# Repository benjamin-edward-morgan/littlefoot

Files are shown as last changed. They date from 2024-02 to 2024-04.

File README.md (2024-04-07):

# littlefoot
This is a repo documenting the modification of an old remote controlled car to include a Raspberry pi, a camera and some sensors that allow it to be teleoperated over a wifi connection. It serves as a testbed for [IOC](https://github.com/benjamin-edward-morgan/ioc), which I am developing as a more general purpose teleoperation software package. 

So they wouldn't go to waste, this project uses some discontinued parts that I just happened to have lying around. The 3d printed parts also are specific to this particular model of RC car and my modifications to it. As such, this should serve as more of an example to inform future designs, rather than something intended to be reproduced identically.

### Overview 
- **[IOC](https://github.com/benjamin-edward-morgan/ioc)**
The core application is implemented in Rust. It serves the mjpeg stream, the websocket, and communicates with the i2c devices.
- **[config](config/README.md)**
Contains the config files for IOC. The config file specifies what hardware is attached and how it is controlled. 
- **[littlefoot-ui](littlefoot-ui/README.md)**
A UI implemented in React and TSX. It connects to the websocket and displays the mjpeg stream, sensor outputs and allows driving and looking. Includes a touch UI for touch capable devices, and a keyboard-based interface for desktop.
- **[parts](parts/README.md)**
Openscad design and `.stl` renders for 3d printed parts used in this build.

| Fully Assembled | Interface |
| --- | --- |
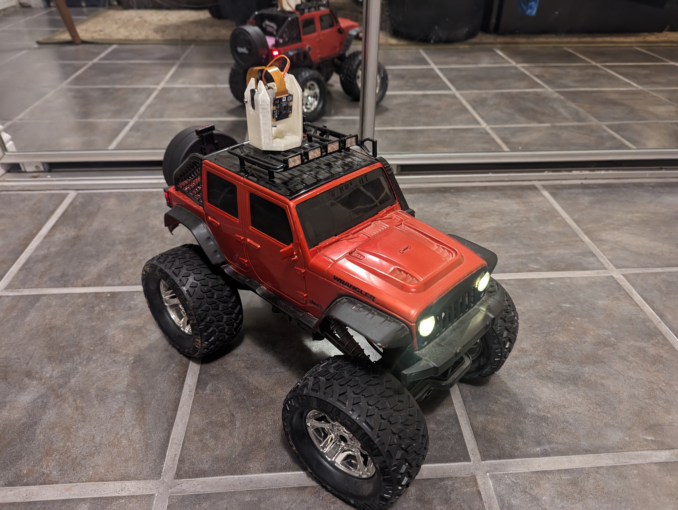
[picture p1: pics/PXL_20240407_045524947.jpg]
littlefoot assembled and running
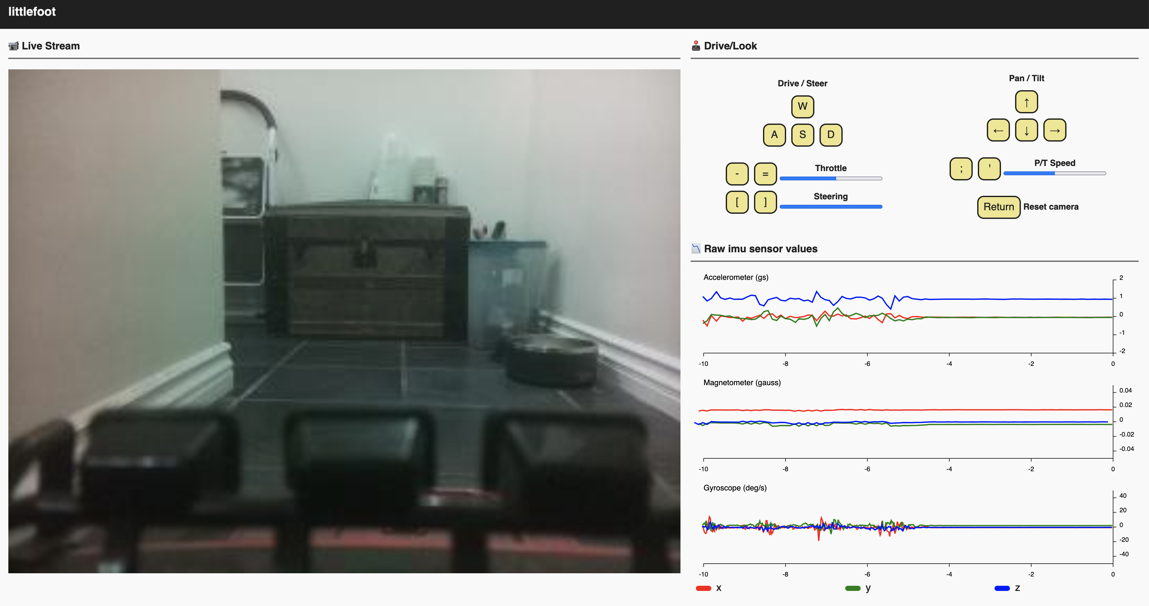
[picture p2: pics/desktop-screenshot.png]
littlefoot-ui interface
|  |  |

### Features 
- Connection over local wifi connection to a web interface
- Live video feed from the camera, in the form of an mjpeg stream
- Camera can be panned and tilted about 180 degrees
- Camera settings can be adjusted in real time
- Accelerometer, Gyroscope and Magenetometer are charted in real time
- Barometric pressure and temperature are displayed in real time (just threw that in there for fun since it was already included on the 10 DOF board)
- Headlights and taillights are independently controllable and dimmable

### Parts list
- 1x old ["New Bright" RC Jeep](https://www.newbright.com/products/rc-heavy-metal-jeep-wrangler/), with exising circuit board removed.
- 1x [Raspberry PI Zero W](https://www.raspberrypi.com/products/raspberry-pi-zero-w/), whith headers soldered on.
- 1x [Raspberry PI Camera V2.1](https://www.raspberrypi.com/products/camera-module-v2/) NoIR and [30cm ribbon rable](https://www.amazon.com/gp/product/B07H3L3LM2/ref=ppx_yo_dt_b_asin_title_o01_s00?ie=UTF8&th=1) for Pi Zero.
- 1x microSD card (overkill at 64gb)
- 3x [18650 batteries](https://www.18650batterystore.com/products/samsung-30q), and [holders](https://www.amazon.com/HiLetgo-10pcs-Battery-Holder-Storage/dp/B00LSG5BKO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)
- 1x [battery protection board](https://www.amazon.com/Battery-Protection-Lithium-Charger-Charging/dp/B09B335Q4P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)
- 1x [DC/DC voltage converter](https://www.sparkfun.com/products/9370) and trim resistor(s) to get 5v
- 1x [PCA9685 breakout](https://www.adafruit.com/product/815) (pwm output)
- 1x discontinued [10 DOF board](https://www.adafruit.com/product/1604) with L3GD20H, LSM303, and BMP180
- 1x [L298N dual h-bridge](https://www.sparkfun.com/products/9479)
- 4x LEDs (2 red and 2 white)
- 3S [battery level indicator](https://www.amazon.com/gp/product/B07T5RBF5V/ref=ppx_yo_dt_b_asin_title_o02_s00?ie=UTF8&th=1) 
- DC Barrel jack and [3S Li-Ion charger](https://www.amazon.com/gp/product/B086ZFHVX9/ref=ppx_yo_dt_b_asin_title_o01_s00?ie=UTF8&psc=1)
- Diodes, resistors and a couple capacitors. 
- Perf board, wire, connectors, crimp connectors, hot glue, 3mm nuts and bolts.
- 3d printed brackets for perf boards, pan/tilt mechanism.

### Learnings (so far...)
- The RC car does not have great meanuverability. It has two discrete steering radii, rathern than a continuous range. The smallest turning radius is still on the order of 1 meter. This is entirely due to New Bright's design of the steering linkage which limits the steering range.
- The capacitor in parallel with the power supply to the L298N is necessary to protect the chip. Once, it ran into a wall at full speed without the capacitor and half of the chip was fried. It was a real pain to replace.
- The old Raspberry Pi V2 camera has a decent field of view, but the new wide angle v3 camera should be better.
- You should take care to not push a servo beyond its limit. On another occasion the pan servo (which should only have a 180 degree range) was pushed too far in one direction. The servo unexpectely performed a full rotation, wrapping the ribbon cable around the camera and tilt mechanism until the servo and camera were unplugged. This unfortunately damaged the ribbon cable and connector on the Raspberry Pi.  
- Would be nice to sense the battery voltage. The only way to get a battery reading is to view the indicator on the physical car. 
- The DC motors for drive and steer do create noticible noise in the magnetometer readings.
- Internal temperature sensor rises about 10 degrees C above ambient when the car is running, due to the heat generated by the Raspberry Pi.

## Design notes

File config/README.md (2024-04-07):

## Config 
- `littlefoot.yml` 
This is the file used on the actual robot with live hardware
- `littlefoot-dev.yml`
This is used for local development. It is compatible with a build of IOC that does not include the hardware drivers.

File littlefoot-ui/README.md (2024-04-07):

### littlefoot-ui 
This is web UI using React that acts as the remote control and shows the camera live feet, telemetry data etc. See [README_VITE.md](README_VITE.md) for more information about vite + react. 

This expects:
- /ws to be an ioc websocket url
- /stream to be an mjpeg stream

It should be packaged with `npm run build` and placed in the `assets` directoy on the raspberry pi, alongside littlefoot.yml and the ioc binary. 

You can also use `npm run dev` and run the IOC sever locally. By default npm will proxy to `localhost:8080` but that can be configured in `vite.config.ts`

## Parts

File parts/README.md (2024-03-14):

### parts 

These are some 3d printed parts I whipped up:
- pan/tilt mechanism based on 1 regular and one micro servo 
- adapter to perf boards to rc jeep body, spacers between perf boards 
- protective plastic parts to enclose another perf board for battery protection board

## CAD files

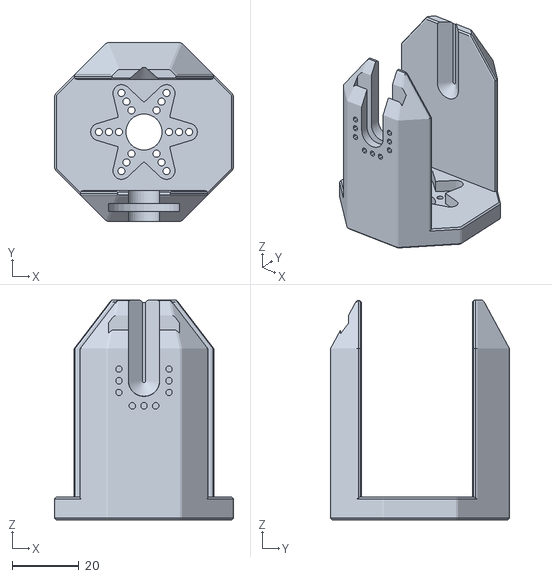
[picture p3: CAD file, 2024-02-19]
parts/stl/pantilt-bracket.stl
53.6 x 53.6 x 65.8

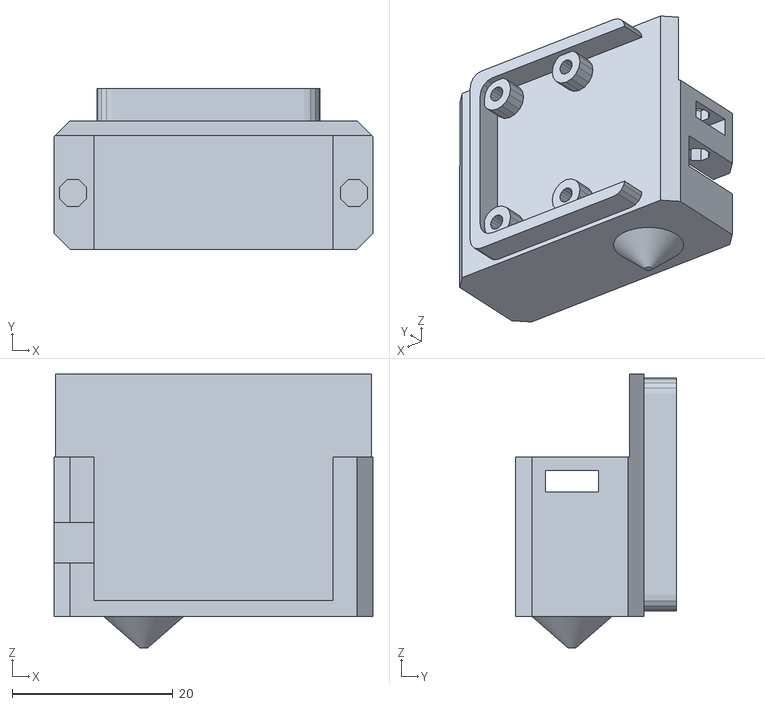
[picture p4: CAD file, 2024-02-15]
parts/stl/cam-bracket.stl
39.8 x 20.0 x 34.1

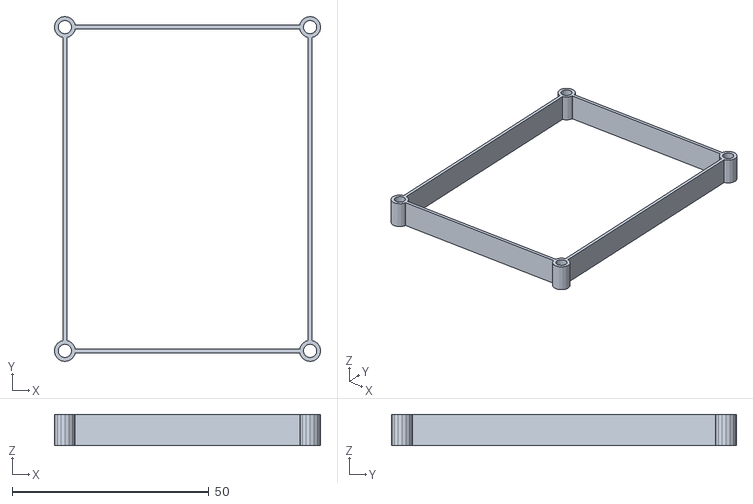
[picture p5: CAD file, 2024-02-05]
parts/stl/spacer1.stl
67.8 x 87.8 x 8.00

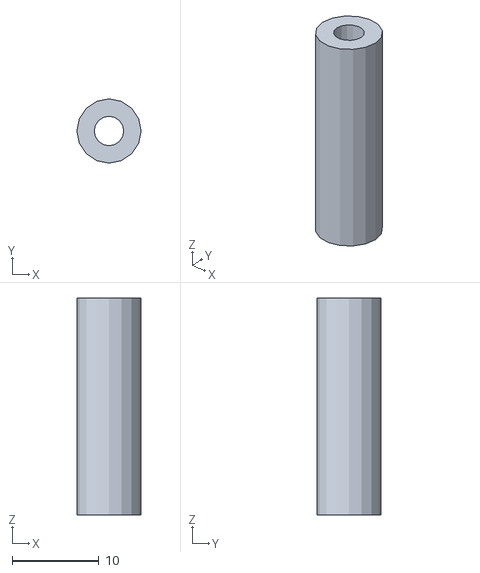
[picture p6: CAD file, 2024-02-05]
parts/stl/spacer.stl
7.40 x 7.40 x 25.0

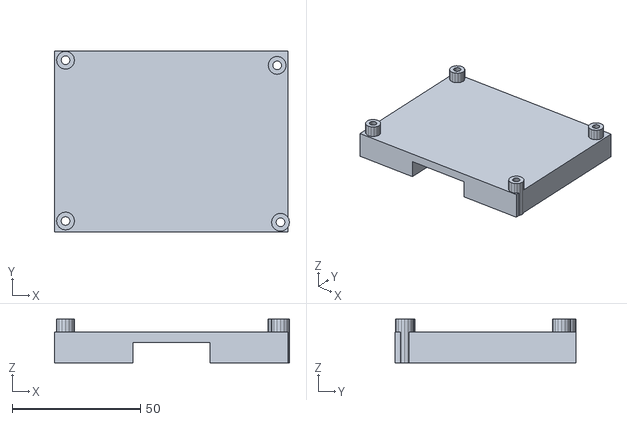
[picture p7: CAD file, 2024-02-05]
parts/stl/power_board_bottom.stl
91.5 x 70.5 x 17.0

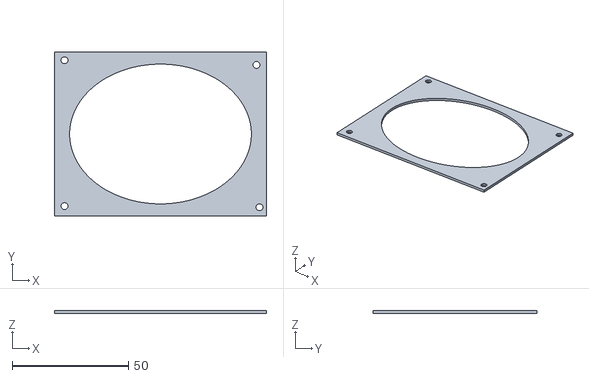
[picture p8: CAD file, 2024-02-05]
parts/stl/board-test.stl
91.0 x 70.5 x 1.20

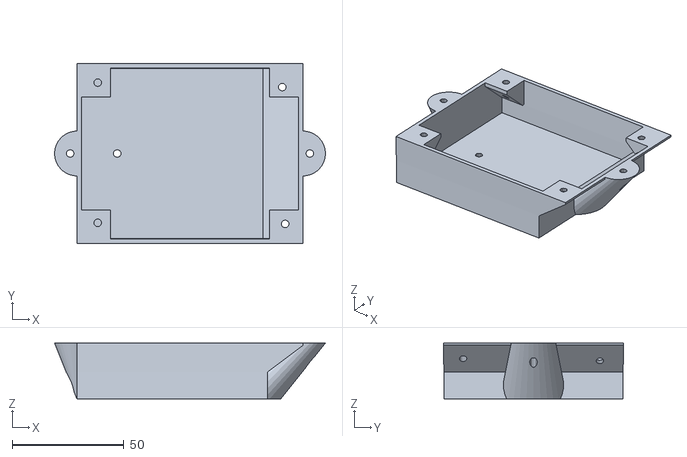
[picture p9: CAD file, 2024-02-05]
parts/stl/electronics-base.stl
121.0 x 80.5 x 25.0

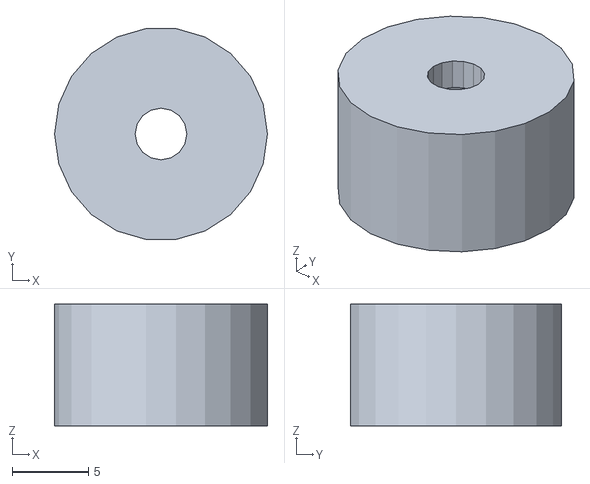
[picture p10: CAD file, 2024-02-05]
parts/stl/captured-nut-test.stl
14.0 x 13.9 x 8.00

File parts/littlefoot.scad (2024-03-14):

//apologies for this sloppy scad code. ~b


//electronics enclosure 
base_w = 80;
base_l = 85;
base_screw_y_offs = 18;
base_screw_d = 3;
base_t = 4;
wall_t = 2;
xy_clearence = 3;
xy_tol = 0.2;

//body (jeep)
body_rear_mount_w = 91;
body_rear_mount_z = 12;
body_rear_mount_x = -80; 
body_front_mount_w = 67;
body_front_mount_z = 32;
body_front_mount_x = 140;
interior_clearence = 52;

//electronics 
perf_board_w = 70.5;
perf_board_l = 91;
perf_board_t = 1.2; 
perf_board_hole_d = 3;
perf_board_holes = [
    [-perf_board_l/2+4.3, -perf_board_w/2+4.3],
    [-perf_board_l/2+4.3, perf_board_w/2-3.6],
    [perf_board_l/2-4.3, perf_board_w/2-5.6],
    [perf_board_l/2-3, -perf_board_w/2+3.8],
];



enclosure_w = perf_board_w + 2*(xy_clearence + wall_t);
enclosure_l = perf_board_l + 2*(xy_clearence + wall_t);
enclosure_x_offs = 8;
enclosure_z_offs = 12;
enclosure_h = 50;

//hardware
bolt_d = 3;
nut_w = 5.4;
nut_r = nut_w/(2*cos(30));
nut_h = 2.27;
nut_tol = nut_h + xy_tol + wall_t;



std_srvo_body_w = 20.33;
std_srvo_body_l = 40.78;
std_srvo_body_h = 38.04;
std_srvo_bracket_l = 55;
std_srvo_bracket_h = 2.9;
std_srvo_hole_a = 10.0;
std_srvo_hole_b = 49.5;
std_srvo_hole_d = 4;
std_srvo_bracket_z = 7.75;
std_srvo_shaft_offs = 10;
std_srvo_keepout_d = 13.5;
std_srvo_keepout_h = 2.25;



module std_servo() {
    color("DimGray")
    difference() {
        union() {
            translate([-std_srvo_shaft_offs, -std_srvo_body_w/2, -std_srvo_body_h])
            cube(size=[std_srvo_body_l,std_srvo_body_w,std_srvo_body_h]);
            
            translate([-std_srvo_shaft_offs - (std_srvo_bracket_l-std_srvo_body_l)/2, -std_srvo_body_w/2, -std_srvo_bracket_h-std_srvo_bracket_z])
            cube(size=[std_srvo_bracket_l,std_srvo_body_w,std_srvo_bracket_h]);
            
            cylinder(r=std_srvo_keepout_d/2, h=std_srvo_keepout_h);
        }
        
        translate([std_srvo_body_l/2 - std_srvo_shaft_offs,0,-std_srvo_bracket_z - 2*std_srvo_bracket_h])
        for(i=[std_srvo_hole_b/2,-std_srvo_hole_b/2])
        for(j=[std_srvo_hole_a/2,-std_srvo_hole_a/2])
        translate([i,j,0])
        cylinder(r=std_srvo_hole_d/2,h=3*std_srvo_bracket_h,$fn=16);
    }
}

std_srvo_flwr_outer_d = 31.6;
std_srvo_flwr_tip_d = 4.8;
std_srvo_flwr_cntr_d = 9;
std_srvo_flwr_t = 2;
std_srvo_flwr_h = 6;
std_srvo_flwr_hole_d1 = 27;
std_srvo_flwr_hole_d2 = 21;
std_srvo_flwr_hole_d3 = 15;
std_srvo_flwr_hole_r = 1.75 / 2;
std_srvo_flwr_shaft_r = 8.4 / 2;
std_srvo_flwr_shaft_r2 = 5.75 / 2;



module std_servo_flower() {

    color("Gainsboro")
    difference() {
    union() {
        translate([0,0,std_srvo_flwr_h-std_srvo_flwr_t])
        linear_extrude(std_srvo_flwr_t) 
        difference() {
            union() {
                for(j=[0,120,240])
                rotate(j)
                for(i=[0,180])
                hull() 
                {
                    rotate(i)
                    translate([std_srvo_flwr_outer_d/2 - std_srvo_flwr_tip_d/2,0,0])
                        circle(r=std_srvo_flwr_tip_d/2, $fn=16);
                    circle(r=std_srvo_flwr_cntr_d/2, $fn=32);
                }
            }
            
            for(j=[0:60:359])
            rotate(j)
            for(i=[std_srvo_flwr_hole_d1/2, std_srvo_flwr_hole_d2/2, std_srvo_flwr_hole_d3/2])
            translate([i,0,0])
            circle(r=std_srvo_flwr_hole_r , $fn=8);
        }
        
        cylinder(r=std_srvo_flwr_shaft_r,h=std_srvo_flwr_h,$fn=16);
    }
    
    translate([0,0,-std_srvo_flwr_h])
    cylinder(r=std_srvo_flwr_shaft_r2, h=std_srvo_flwr_h * 3,$fn=16);
    }

}


mro_srvo_body_w = 14;
mro_srvo_body_l = 29.4;
mro_srvo_body_h = 28;
mro_srvo_bracket_l = 39.75;
mro_srvo_bracket_h = 2.4;
mro_srvo_hole_a = 35;
mro_srvo_hole_d = 4;
mro_srvo_bracket_z = 7.7;
mro_srvo_shaft_offs = 6;
mro_srvo_keepout_d = 8.7;
mro_srvo_keepout_h = 3;


module micro_servo() {
    color("Gray")
    difference() {
        union() {
            translate([-mro_srvo_shaft_offs, -mro_srvo_body_w/2, -mro_srvo_body_h])
            cube(size=[mro_srvo_body_l,mro_srvo_body_w,mro_srvo_body_h]);

            translate([-mro_srvo_shaft_offs - (mro_srvo_bracket_l-mro_srvo_body_l)/2, -mro_srvo_body_w/2, -mro_srvo_bracket_h-mro_srvo_bracket_z])
            cube(size=[mro_srvo_bracket_l,mro_srvo_body_w,mro_srvo_bracket_h]);

            cylinder(r=mro_srvo_keepout_d/2, h=mro_srvo_keepout_h);
        }


        translate([mro_srvo_body_l/2 - mro_srvo_shaft_offs,0,-mro_srvo_bracket_z - 2*mro_srvo_bracket_h])
        for(i=[mro_srvo_hole_a/2,-mro_srvo_hole_a/2])
        translate([i,0,0])
        cylinder(r=mro_srvo_hole_d/2,h=3*mro_srvo_bracket_h,$fn=16);
    }          
}

mro_srvo_disk_r = 21/2;
mro_srvo_disk_t = 2;
mro_srvo_disk_h = 5.6;
mro_srvo_disk_hole_r = 1.5/2;
mro_srvo_disk_hole_a = 15;
mro_srvo_disk_hole_b = 7;
mro_srvo_disk_center_r = 9/2;
mro_srvo_disk_center_hole_r = 2;


module micro_servo_disk() {

    color("silver")
    difference() {
        union() {
            translate([0,0,mro_srvo_disk_h-mro_srvo_disk_t])
            linear_extrude(mro_srvo_disk_t)
            difference() {
                circle(r=mro_srvo_disk_r, $fn = 16);

                for(j=[0,90,180,270])
                for(i=[-mro_srvo_disk_hole_b/2,0,mro_srvo_disk_hole_b/2])
                rotate(j)
                translate([mro_srvo_disk_hole_a/2, i])
                circle(r=mro_srvo_disk_hole_r, $fn=8);
            }
            
            cylinder(r=mro_srvo_disk_center_r,h=mro_srvo_disk_h,$fn=16);
        }
        
        translate([0,0,-mro_srvo_disk_h])
        cylinder(r=mro_srvo_disk_center_hole_r,h=mro_srvo_disk_h*3,$fn=16);
    }

}

rpi_cam_2_board_w = 25;
rpi_cam_2_board_h = 23.862;
rpi_cam_2_board_t = 1;
rpi_cam_2_board_corner_r = 2.0;
rpi_cam_2_board_hole_r = 1.1;
rpi_cam_2_board_hole_a = 2;
rpi_cam_2_board_hole_b = 2;
rpi_cam_2_board_hole_c = 14.5;
rpi_cam_2_sensor_wl = 8.5;
rpi_cam_2_sensor_h = 5.75;
rpi_cam_2_bottom_sensor_offs = 9.462;
rpi_cam_2_connector_w = 22;
rpi_cam_2_connector_h = 5.6;
rpi_cam_2_connector_t = 2.75;



module rpi_cam_2() {
    
    color("OliveDrab")
    linear_extrude(rpi_cam_2_board_t)
    difference() {
        hull() {
            for(i=[rpi_cam_2_board_w/2 - rpi_cam_2_board_corner_r, -rpi_cam_2_board_w/2 + rpi_cam_2_board_corner_r])
            for(j=[- rpi_cam_2_board_corner_r, -rpi_cam_2_board_h + rpi_cam_2_board_corner_r])
            translate([i,j,0])
            circle(r=rpi_cam_2_board_corner_r, $fn=16);
        }
    
        for(i=[rpi_cam_2_board_w/2 - rpi_cam_2_board_hole_a, -rpi_cam_2_board_w/2 + rpi_cam_2_board_hole_a])
        for(j=[-rpi_cam_2_board_hole_b, -rpi_cam_2_board_hole_c])
        translate([i,j,0])
        circle(r=rpi_cam_2_board_hole_r, $fn=16);
    }
    
    color("DarkSlateGray")
    translate([-rpi_cam_2_sensor_wl/2,-rpi_cam_2_sensor_wl/2 - rpi_cam_2_board_h + rpi_cam_2_bottom_sensor_offs ,rpi_cam_2_board_t])
    cube(size=[rpi_cam_2_sensor_wl,rpi_cam_2_sensor_wl,rpi_cam_2_sensor_h]);

    color("LightSlateGray") 
    translate([-rpi_cam_2_connector_w/2,-rpi_cam_2_board_h,-rpi_cam_2_connector_t])
    cube([rpi_cam_2_connector_w,rpi_cam_2_connector_h,rpi_cam_2_connector_t]);
}


pt_srvo_displacement = [0,-15,45];
pt_srvo_rotation = [90,90,0];

cam_displacement = [20,12,pt_srvo_displacement[1]];
cam_rotation = [0,-90,-90];


cam_brck_corner_r = 2;
cam_brck_t = 2;
cam_brck_h = mro_srvo_body_h + xy_tol + cam_brck_t;
cam_brck_pad_d = 5;

cam_brck_nbbn_r1 = 5;
cam_brck_nbbn_r2 = 0.5;
cam_brck_nbbn_h = 4;


//camera_bracket();

module camera_bracket() {

color("purple")
    union() {
    difference() {
    translate([0,0,-cam_brck_h])
    linear_extrude(cam_brck_h)
    translate([-mro_srvo_shaft_offs - (mro_srvo_bracket_l - mro_srvo_body_l) / 2 + cam_brck_corner_r,-mro_srvo_body_w/2 + cam_brck_corner_r])
    minkowski() {
        square(size=[mro_srvo_bracket_l - 2*cam_brck_corner_r, mro_srvo_body_w  - 2*cam_brck_corner_r + cam_brck_t] );
        circle(r=cam_brck_corner_r,$fn=4);
    }
    
    translate([-mro_srvo_shaft_offs-xy_tol,-mro_srvo_body_w/2-xy_tol,-mro_srvo_body_h-xy_tol])
    cube(size=[mro_srvo_body_l+2*xy_tol, mro_srvo_body_w+2*xy_tol, mro_srvo_body_h+2*xy_tol]);
    
    translate([-mro_srvo_shaft_offs - (mro_srvo_bracket_l - mro_srvo_body_l) / 2-xy_tol,-mro_srvo_body_w/2 - xy_tol,-mro_srvo_bracket_z-mro_srvo_bracket_h-xy_tol])
        cube(size=[mro_srvo_bracket_l + 2*xy_tol,mro_srvo_body_w+2*xy_tol,mro_srvo_bracket_h+2*xy_tol + 10]);
    
        for(i=[-mro_srvo_hole_a/2,mro_srvo_hole_a/2])
    translate([i + mro_srvo_body_l/2 - mro_srvo_shaft_offs  ,0, -14.5])
    nut_negative_2();
    
        translate([-15,-10,7-mro_srvo_body_h-2.5])
    cube([10,15,5]);
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

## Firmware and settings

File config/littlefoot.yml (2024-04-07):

metadata:
  name: littlefoot
  description: just a remote controlled car powered by raspberry pi

# modules expose inputs and outputs from various sources
modules:
# server that exposes websocket endpoint, mjpeg stream, and static files
  local_server: 
    Server:
      port: 8080
      root_context: /
      inputs:
        drive:
          Float: { start: 0.0, min: -1, max: 1, step: 0.0009765625 }
        steer:
          Float: { start: 0.0, min: -1, max: 1, step: 0.0009765625 }
        pan: 
          Float: { start: 0, min: -1, max: 1, step: 0.0009765625 }
        pan_trim: 
          Float: { start: 0.0400390625, min: -1, max: 1, step: 0.0009765625 }
        tilt: 
          Float: { start: 0, min: -1, max: 1, step: 0.0009765625 }
        tilt_trim: 
          Float: { start: 0.7587890625, min: -1, max: 1, step: 0.0009765625 }
        headlights:
          Float: { start: 0.5, min: 0, max: 1, step: 0.1 }
        taillights:
          Float: { start: 0.0, min: 0, max: 1, step: 0.1 }
        enable_camera:
          Bool: { start: true }
        mjpeg_quality:
          Float: { start: 75, min: 0, max: 100, step: 1 }
        camera_framerate:
          Float: { start: 10, min: 1, max: 60, step: 1 }
        camera_resolution:
          String: 
            start: "320x240"
            max_length: 12
            choices: 
              "320x240": "320x240"
              "640x480": "640x480"
              "1280x720": "1280x720"
              "1920x1080": "1920x1080"
        camera_tuning_file:
          String:
            start: "/usr/share/libcamera/ipa/rpi/vc4/imx219_noir.json"
            max_length: 1024
            choices:
              "none": ""
              "RpiCameraV2": "/usr/share/libcamera/ipa/rpi/vc4/imx219.json"
              "RpiCameraV2 - NoIR": "/usr/share/libcamera/ipa/rpi/vc4/imx219_noir.json"
              "Uncalibrated": "/usr/share/libcamera/ipa/rpi/vc4/uncalibrated.json"
      outputs:
        gyroscope: Array
        magnetometer: Array
        accelerometer: Array
        temperature: Float 
        pressure: Float 
        jpeg_frames: Binary
      endpoints: 
        "/": 
          Static:
            directory: "assets"
        "/ws":
          WebSocket: 
            inputs: [ 
              pan, tilt, pan_trim, tilt_trim, 
              drive, steer, 
              headlights, taillights, 
              enable_camera, mjpeg_quality, camera_framerate, camera_resolution, camera_tuning_file
            ]
            outputs: [ 
              gyroscope, magnetometer, accelerometer, 
              temperature, pressure
            ]
        "/stream":
          Mjpeg:
            output: jpeg_frames

  # pwm signals used to drive various hardware components
  pwm:
    Pca9685:
      i2c_bus: 0
      i2c_address: 0x40
      channels:
        pan_servo: 0
        tilt_servo: 1
        headlights: 2
        taillights: 3
        drive_enable: 4
        drive_rev: 5
        drive_fwd: 6
        steer_enable: 7
        steer_left: 8
        steer_right: 9

  # a camera
  camera:
    RaspiCam: {}

  # atmospheric pressure and temperature sensor
  press_temp:
    Bmp180:
      pressure_precision: Standard
      period_ms: 1000

  # mems gyroscope sensor
  gyro:
    L3dg20:
      i2c_address: 0x6B
  
  # combined magnetometer and accelerometer sensor
  mag_accel:
    Lsm303dlhc: {}

# transformers read from one or more inputs and produce one or more new inputs
transformers:

  # adds pan/tilt with respective trim values 
  pan_sum:
    Sum:
      inputs:
        - local_server.pan
        - local_server.pan_trim
  
  tilt_sum:
    Sum:
      inputs:
        - local_server.tilt
        - local_server.tilt_trim

  tilt_clamp:
    Clamp:
      input: tilt_sum.value
      min: -1
      max: 1

  pan_clamp:
    Clamp:
      input: pan_sum.value
      min: -1
      max: 1

  # transforms pan/tilt values to values compatible with servos 
  # assuming 60hz, 0.05 and 0.15 duty cycle are roughly 0 and 180 degrees
  tilt_servo: 
    LinearTransform:
      input: tilt_clamp.value 
      from: [-1, 1]
      to: [0.05, 0.12]
  
  pan_servo: 
    LinearTransform:
      input: pan_clamp.value
      from: [-1, 1]
      to: [0.05, 0.15]

  # hbridges rectify drive and steer values and create "enabled" signals 
  # when the input is nonzero. This is becuase electrically, there are 
  # hbridges controlling a reversible DC current throug the drive and steer motors.
  drive_hbridge:
    HBridge:
      input: local_server.drive 
  
  steer_hbridge:
    HBridge:
      input: local_server.steer

# pipes read from inputs and write to outputs
pipes:
# camera pan/tilt
  - { from: pan_servo.value, to: pwm.pan_servo }
  - { from: tilt_servo.value, to: pwm.tilt_servo }
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

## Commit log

2024-02-05 first littlefoot commit
    [board-test.stl, captured-nut-test.stl, electronics-base.stl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]
2024-02-15 wip pan til cam bracket
    [cam-bracket.stl, littlefoot.scad]
2024-02-19 pantilt, more improvements
    [littlefoot.scad, pantilt-bracket.stl]
2024-02-29 wip add sensor data
2024-03-14 little tweaks for vector outputs
    [littlefoot.scad]
2024-04-03 tweaks, adding camera controls
2024-04-07 make sure to clamp pan/tilt in keyboard ui
